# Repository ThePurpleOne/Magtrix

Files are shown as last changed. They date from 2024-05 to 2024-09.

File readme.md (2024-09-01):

---
Author : Jonas Stirnemann
Date : 2024
Title : Magnetic Board Game
Description : Board game etched directly on a PCB (Chess, Tic-Tac-Toe, etc.)
---

# Tic Tac Toe Board Game

PCB design for a Tic Tac Tie game. The game is played on a 3x3 grid, where the players have to align 3 of their pieces in a row, column or diagonal to win. The pieces are actual magnets that are moved by activating coils etched on the PCB.

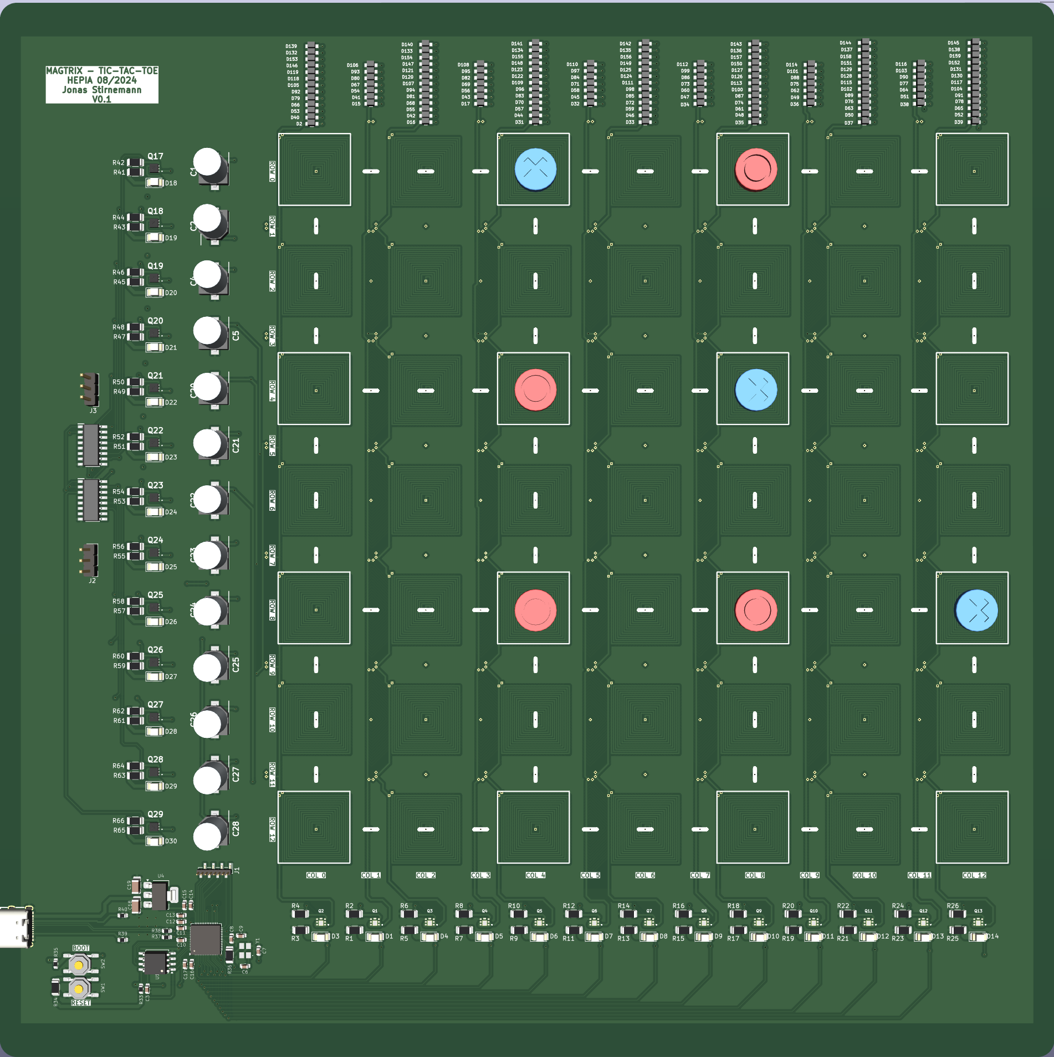
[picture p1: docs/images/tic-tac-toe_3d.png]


## Front end

The front end in React will display the game board and let the users play the game. The code can be found in [src/web/tictactoe/frontend](src/web/tictactoe/frontend)

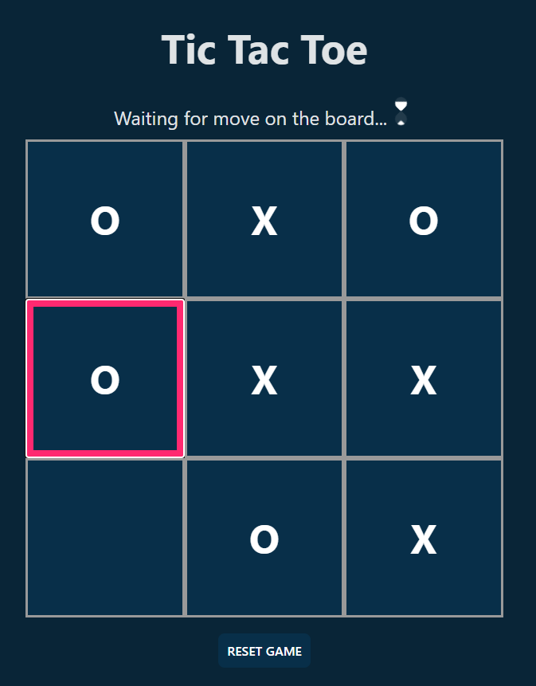
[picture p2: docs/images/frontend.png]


## Back end

The back end in Python will handle the communication with the actual board to tell it to make the moves and wait for an acknowledgement. The code can be found in [src/web/tictactoe/backend](src/web/tictactoe/backend)

## MCU Firmware

The firmware for the MCU will handle the communication with the back end to receive the moves. It will control the coils to move the pieces and tell the backend back when the move is done. The code can be found in [src/mcu/tictactoe](src/mcu/tictactoe)

## PCB

The PCB design is made in KiCad and can be found in [pcb/magtrix](pcb/magtrix)

Here's the schematics:

[docs/images/magtrix.pdf](docs/images/magtrix.pdf)

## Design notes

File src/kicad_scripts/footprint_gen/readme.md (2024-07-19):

# Footprint generation

This is a simple script to 2 types of coils with given parameters.

## Parameters

> Note : The coils are square.

- side_width: Width of the coil in both x and y direction.
- line_width: Width of the traces in the coil.
- spacing : Spacing between the traces.

> Note : The number of coils is determined by the side_width and spacing.

## Usage

The script can generate coils with specified layers.

The best choice on a 4 layer board is to use the top and third layers
for the main coils and second and bottom layers for the sub coils.
In a "sandwiched" configuration

```python
from square_coil import Coiler
if __name__ == "__main__":
    coiler = Coiler(side_width=8, line_width=0.3, spacing=0.2)

    coiler.create_and_save(
        name="coil",
        description="Test Coil",
        filename="top_coil",
        output_dir="outputs",
        layers=["F.Cu", "In2.Cu"],
    )

    coiler.create_and_save(
        name="coil",
        description="Test Coil",
        filename="sub_coil",
        output_dir="outputs",
        layers=["In1.Cu", "B.Cu"],
    )
```

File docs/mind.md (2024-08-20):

# Think 

- Add the characteristics that can be moved to enhance the torque
- why not use repulsion or both
- WHAT MAGNETS ??? Why not other Magnets, cubic better polarization for example 
- Multiple coils current direction

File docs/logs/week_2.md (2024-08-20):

---
Title : Week 2
Date : 21/05/2024 - 24/05/2024
---

# Question 1 : Are halbach array really usefull in our case ?

[https://www.duramag.com/techtalk/halbach-arrays/benefits-and-drawbacks-to-using-halbach-arrays/](https://www.duramag.com/techtalk/halbach-arrays/benefits-and-drawbacks-to-using-halbach-arrays/)

# Question 2 : Compute the distance a magnet could be attracted at, using a certain coil.
- Need to compute the magnetic field (B) generated by a coil with a specific current at a specific spot.
- Get the magnet's moment (m) and the distance, looks like we can get it from datasheet or by calculating it. [https://www.e-magnetica.pl/doku.php/magnetic_dipole_moment](https://www.e-magnetica.pl/doku.php/magnetic_dipole_moment)
- Should be able to compute the force from the coil on the magnet
- Shear force is different from adhesion force [https://www.supermagnete.ch/fre/faq/Quelle-est-la-difference-entre-force-d-adherence-et-force-de-cisaillement-force-de-deplacement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](https://www.supermagnete.ch/fre/faq/Quelle-est-la-difference-entre-force-d-adherence-et-force-de-cisaillement-force-de-deplacement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)

# Question 3 : Influence of the coil's shape on the magnetic field
- More turn means more magnetic field but also more resistance thus less current for the same voltage.
- The shape of the coil seems to influence the magnetic field, look for sources ?
- The coil's shape also influences the direction of the magnetic field, could we use that to our advantage ?

# Question 4 : Are linear line coils optimal ?
- The movement are freeer in linear line coils, but it would be harder to know where the magnet exactly are and it would be harder, not to grab other magnets when moving any one.

# MAGNETS

[https://www.supermagnete.ch/fre/aimants-disques-neodyme/disque-magnetique-10mm-1.5mm_S-10-1.5-N](https://www.supermagnete.ch/fre/aimants-disques-neodyme/disque-magnetique-10mm-1.5mm_S-10-1.5-N)

# COIL GENERATION IN KICAD
We can use a simple plugin integrated in Kicad to generate a coil with desired parameters. 

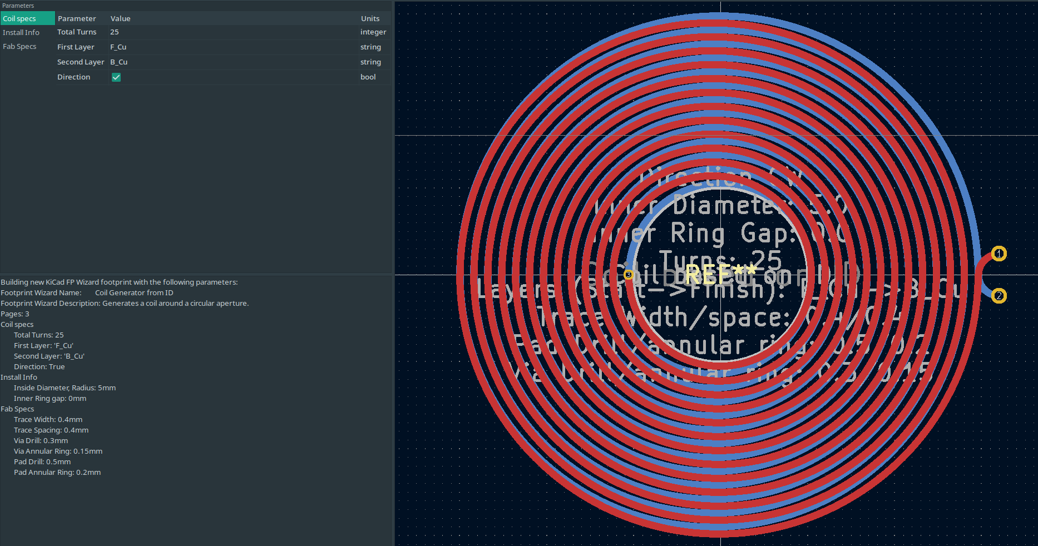
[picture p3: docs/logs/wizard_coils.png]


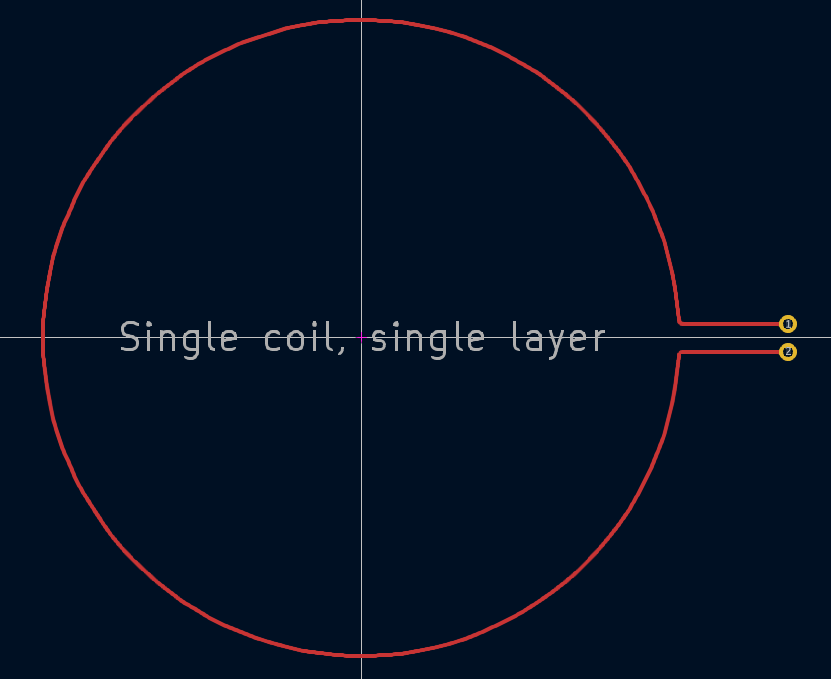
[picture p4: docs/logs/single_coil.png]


## Simulation
With the help of `kiutils` library, we can export the points forming the footprints of the coil.

> Here's an image of a simple coil with only 1 turn.
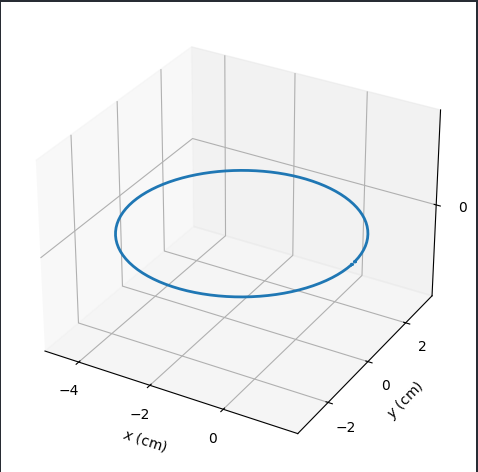
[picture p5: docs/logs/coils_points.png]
Image of points
> 

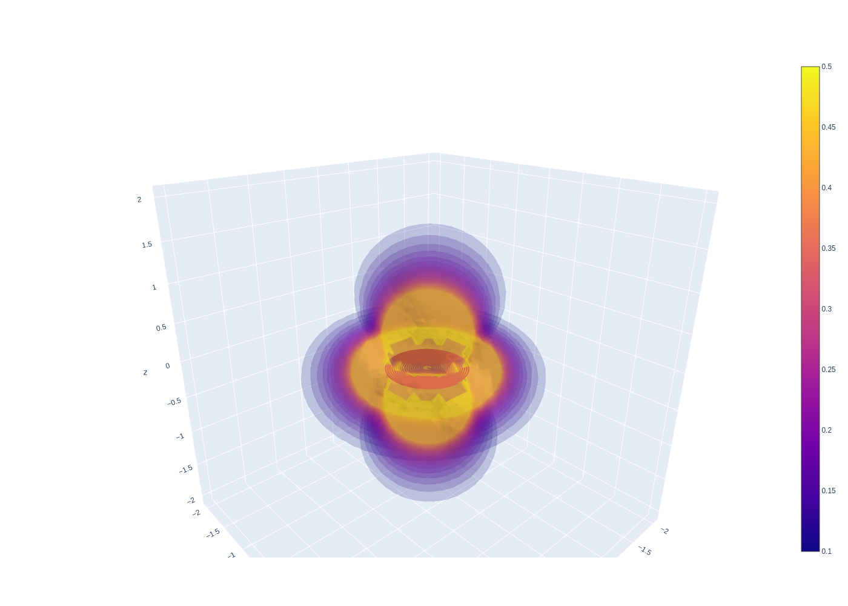
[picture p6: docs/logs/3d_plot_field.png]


## Helmholtz coils

[https://en.wikipedia.org/wiki/Helmholtz_coil](https://en.wikipedia.org/wiki/Helmholtz_coil)

# GENERAL sources
[Encyclopedia](https://www.e-magnetica.pl/doku.php/start)

[Selfmoving Chess Piece Pawn Makes Room](https://www.youtube.com/shorts/qu3ETY4ECMg
)

[Lab 5: The Biot-Savart law - magnetic
fields due to current carrying coils](http://www.yorku.ca/marko/PHYS2211/Lab5.pdf)

[Lorentz Force Law and Biot-Savart](https://andrealommen.github.io/PHY309/lectures/lorentz)

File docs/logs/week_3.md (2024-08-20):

---
Title : Week 3
Date : 28/05/2024 - 31/05/2024
---

# Breadboard proto for linear coils tests

I've made a simple schematics and mounted it on a breadboard to test the coils.

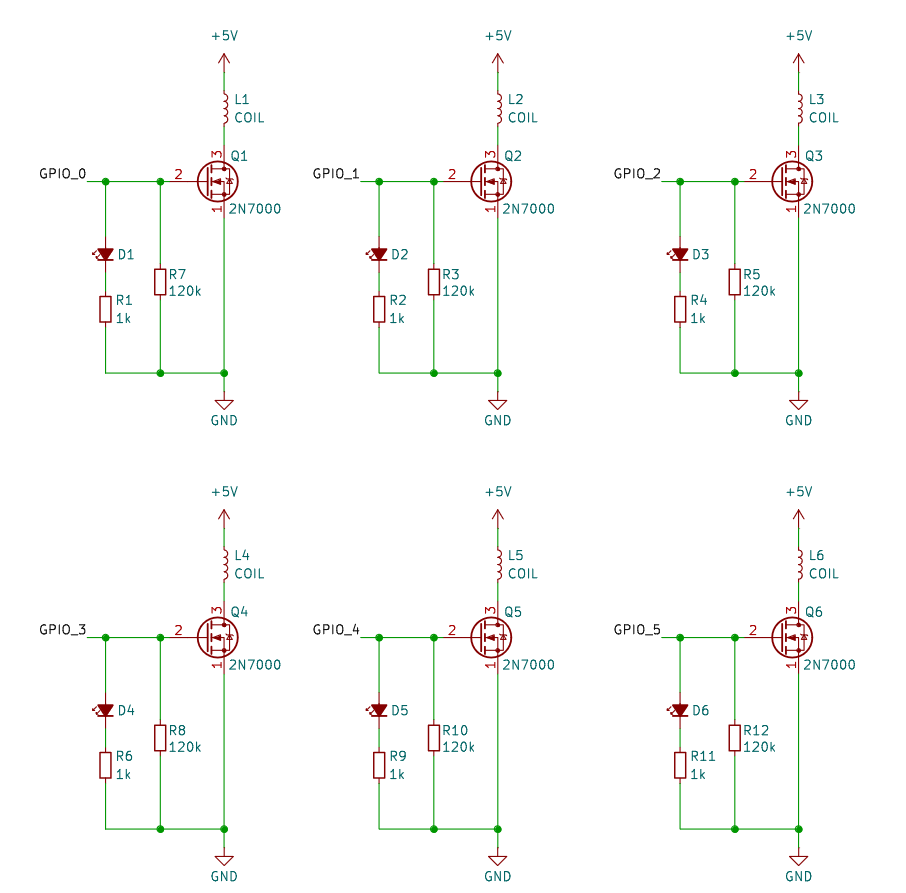
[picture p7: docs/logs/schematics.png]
Schematics


I mounted it with some 2N7000 Q1 N-Channel MOSFETs, controlled via a Raspberry Pi Pico.

```py
import digitalio
import board
import time

pins = [board.GP0, board.GP1, board.GP2, board.GP3, board.GP4, board.GP5, ]

coils = [digitalio.DigitalInOut(pin) for pin in pins]

for coil in coils:
	coil.direction = digitalio.Direction.OUTPUT

coils[3].value = True

print("STARTING TEST")
while True:
	# Set coils 0 to 2 to true one at the time
	for i in range(3):
		coils[i].value = True
		print(f"Coil {i} ON")
		time.sleep(0.3)
		coils[i].value = False
		print(f"Coil {i} OFF")

```

I could see the magnet jitter a bit but without moving, I tried cranking the power up. But aparts from heating more, it did not move better. The fets were getting hot because they were not dimensioned for the current. So i tried with bigger ones. 

I then tried with IRLZ14 N-Channel MOSFETs, but the results were the same. I stopped the test to avoid damaging the power supply and the transistors because i did not have proper flyback diodes.

# Began schematics with driver + flyback diodes and round coils

## Needs
I need:
- Big transistors capable of handling the current
- Flyback diodes to protect over voltage
- Series diodes with the coils to protect the power supply from the back EMF
- Optocouplers to isolate the driver from the Raspberry Pi Pico

## Choices

### Transistors MDD50N03D

I chose the MDD50N03D N-Channel MOSFETs:
- 38 W power dissipation
- 50 A continuous drain current
- 150 A pulsed drain current
- 30 V drain-source voltage

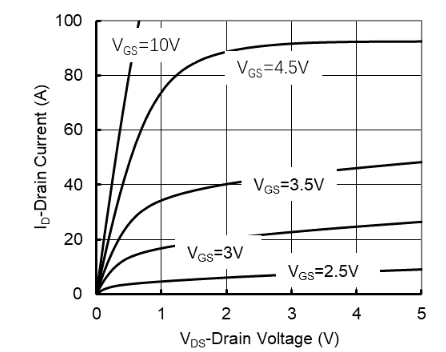
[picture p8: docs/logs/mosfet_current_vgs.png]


With a VGS of 3.3V outputed by the, we can obtain around 20 Amps of current with 0 ohm resistance...

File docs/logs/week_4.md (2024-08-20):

---
Title : Week 3
Date : 04/06/2024 - 07/06/2024
---

# Breadboard proto for linear coils with diodes

I just noticed that the transistors i was using were mixed and some of them were PMOS and others NMOS... 

I remade the schematics and mounted it on a breadboard to test the coils with only the PMOS, sadly...

PMOS is the **IRF9Z34**. 

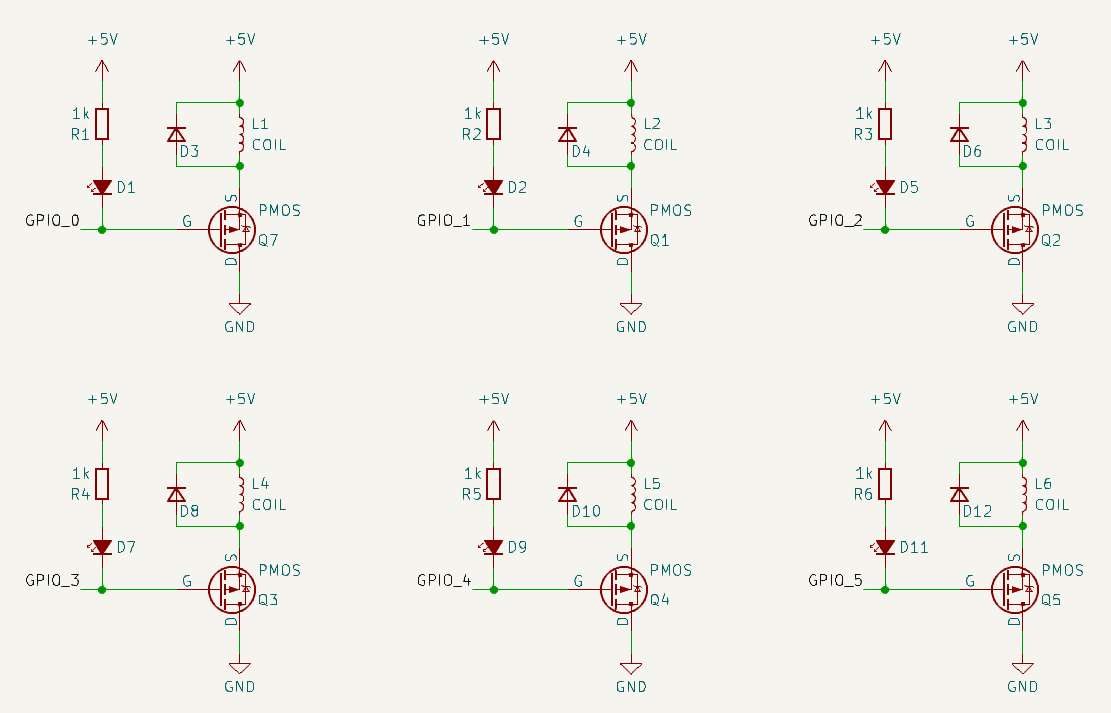
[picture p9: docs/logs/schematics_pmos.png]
Schematics


Pinout of the PMOS : 

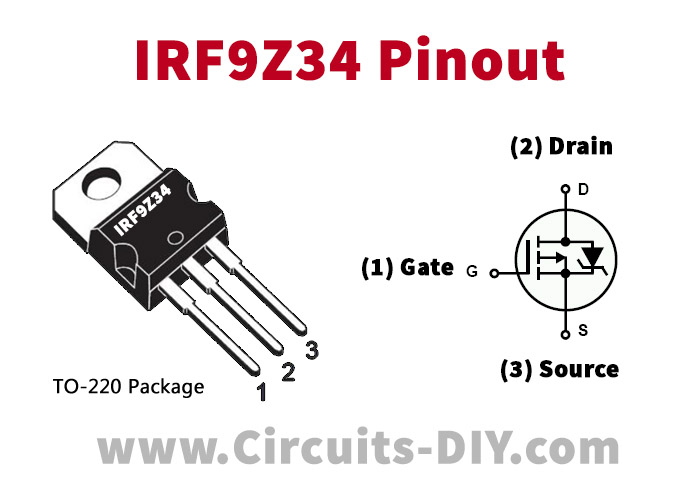
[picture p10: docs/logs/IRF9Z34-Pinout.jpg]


The magnet is moving with a delay of 0.3 between each coil activation. On the small board from PEMi Tech.

[https://hackaday.io/project/154496-2d-actuator-move-micro-robot-in-xy-2d-space](https://hackaday.io/project/154496-2d-actuator-move-micro-robot-in-xy-2d-space)

```py
import digitalio
import board
import time

pins = [board.GP0, board.GP1, board.GP2, board.GP3, board.GP4, board.GP5, ]

coils = [digitalio.DigitalInOut(pin) for pin in pins]

for coil in coils:
	coil.direction = digitalio.Direction.OUTPUT

coils[3].value = True

print("STARTING TEST")
while True:
	# Set coils 0 to 2 to true one at the time
	for i in range(3):
		coils[i].value = False
		print(f"Coil {i} ON")
		time.sleep(0.3)
		coils[i].value = True
		print(f"Coil {i} OFF")
```

But it's moving quiete poorly at low power: 5V (depending on the resistance)

When i crank the power up (10V and the coils draw about 1A), the magnet is moving better but the transistors are getting really hot and i have to stop the test to avoid damaging them.

From what i calculated, with 10V and 1A, the power dissipated by the transistors is 10W.



With this transistor, with a junction to ambient resistance of about 60 °C/W, the temperature should get to more than 600°C lol   

# Old PCB testing

I detached on part of the old PCB to test the it. It was not maintained properly,there was hot glue holding it together and some wires were soldered by hand

# PCB design

## Resistance of the round coils

In order to get a proper transistor that can handle the power, i need to know the resistance of the coils.

I compute the lenght of the spiral with the archimedean spiral formula on a website [https://www.omnicalculator.com/math/spiral-length](https://www.omnicalculator.com/math/spiral-length):

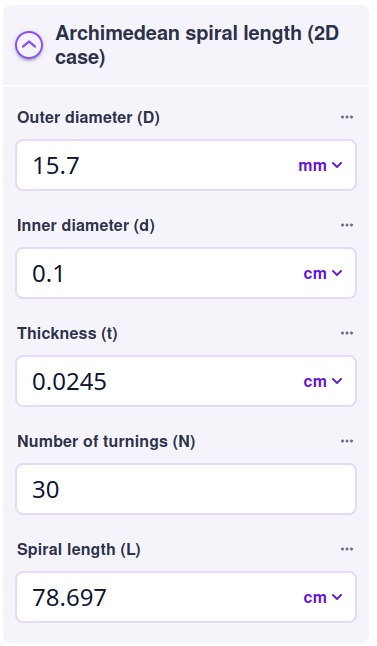
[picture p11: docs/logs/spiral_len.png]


We have a lenght of `78.697` cm for the spiral.

I can now compute the approximate resistance with an online calculator [https://www.allaboutcircuits.com/tools/trace-resistance-calculator/](https://www.allaboutcircuits.com/tools/trace-resistance-calculator/)

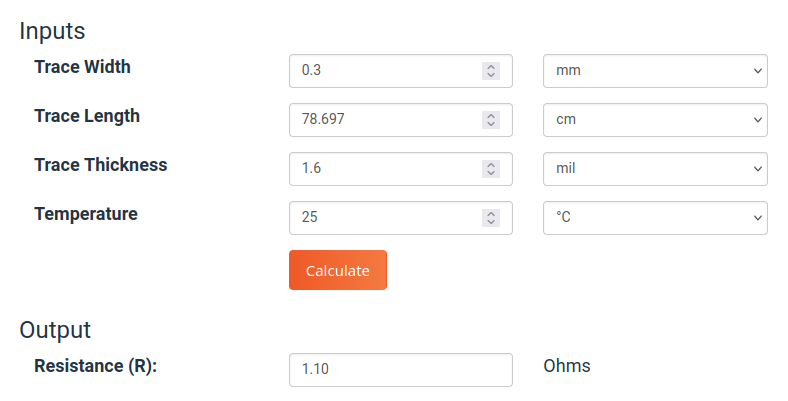
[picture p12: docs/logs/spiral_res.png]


The resistance is about `1.1 ohm`. Taking the via and traces coming to the coil into account, i can approximate the resistance to maximum `10 ohms` and minimum `1 ohm`.

We want to have a maximum amount of power in the coil while still not burning the transistors.

From what i've seen, power transistors have a junction to ambient resistance

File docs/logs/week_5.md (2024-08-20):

---
Title : Week 5
Date : 11/06/2024 - 14/06/2024
---

The 8mm circle magnets only move when applying massive power to the coils (50W...) and i cannot test properly since the transistors are getting really hot.

The 2mm square magnets are moving with 20W but the transistors are getting hot too.

# Solution 1
Find a transistor system that can handle the power, maybe add a heatsink.

# Solution 2
Find smaller magnet (preferably circle) that can be moved with less power. 

# Solution 3 ?
Multiple magnets in a 3d printed piece ? rom what

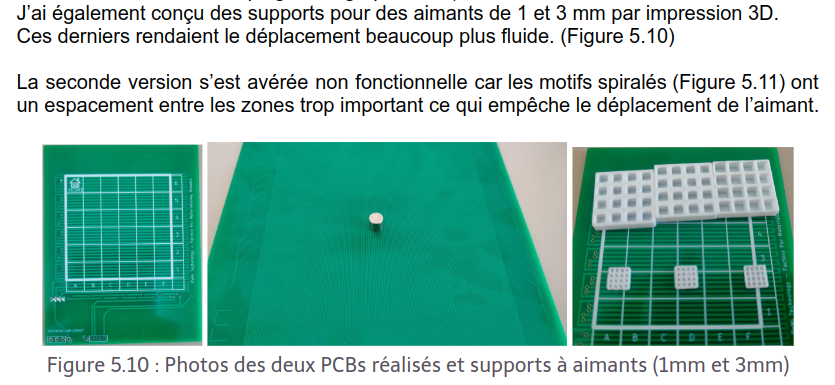
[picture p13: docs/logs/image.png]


# Insane planar motors from Rockwell

[Video demo planar motor](https://www.youtube.com/watch?v=xM1i5vORH4k)

[Actual planar motor site](https://planarmotor.com/en/overview)

# Some papers about 2d XY planar motors
[Papers directory](PAPERS/)

# PCB Specifications

- 2 or 4 layer board depending on possible thickness
- 6 driver transistors
- 4 different coil designs for testing
- Each design can access the 6 transistors
- 10x10mm coil areas

## Coil design 1
- Only 2 different coils per layer (A and B for layer 1 and C, D for layer 2 same as bobricius)
- **10** mils gaps and **20** mils traces (same as bobricius)

## Coil design 2
- 3 different coils per layer (A, B, C for layer 1 and D, E, F for layer 2)
- **10** mils gaps and **20** mils traces (same as bobricius)

## Coil design 3
- Only 2 different coils per layer (A and B for layer 1 and C, D for layer 2 same as bobricius)
- **10** mils gaps and **40** mils traces (same as bobricius)

## Coil design 4
- Only 2 different coils per layer (A and B for layer 1 and C, D for layer 2 same as bobricius)
- **40** mils gaps and **40** mils traces (same as bobricius)

# Components choice

## Transistors

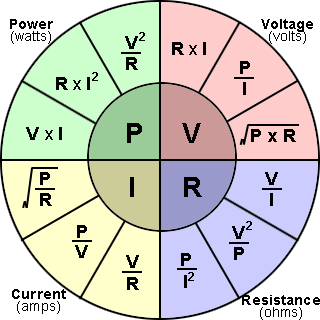
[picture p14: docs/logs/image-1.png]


With the `BUK6D120-40EX` transistor, rdson at 250 ohm:
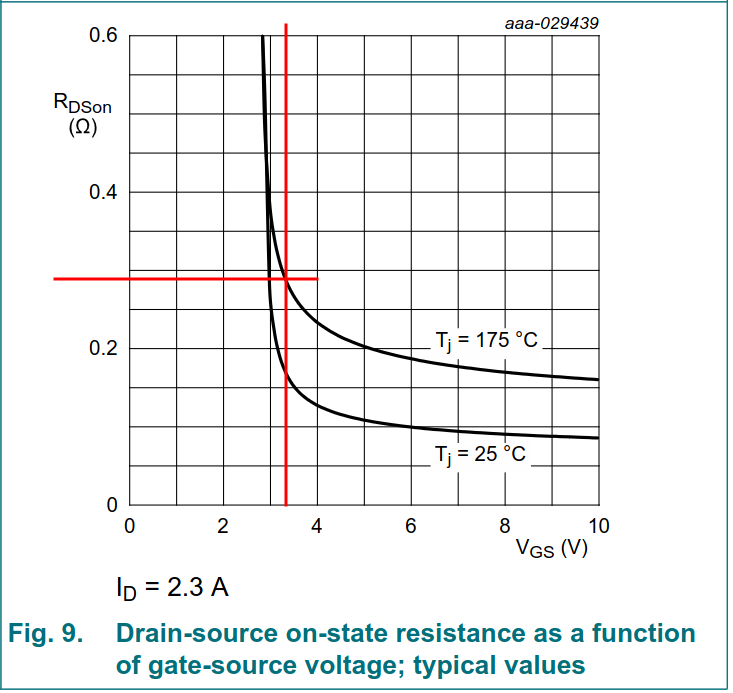
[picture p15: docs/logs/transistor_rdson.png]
RDS ON BUK6D120-40EX


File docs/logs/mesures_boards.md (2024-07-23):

# Sub coils
> Round sub coils between the main coils.

Drawing lots of current at 100%, reduced to 60-70% with a PWM 

Max temperature : 80°C (Thermal camera)

8mm Magnet 

## Code
```py
import digitalio
import board
import time
import pwmio

pins = [board.GP0, board.GP1, board.GP2, board.GP3, board.GP4, board.GP5, ]

coils = [pwmio.PWMOut(pin, frequency=50000) for pin in pins]

for coil in coils:
    coil.duty_cycle = 0

print("STARTING TEST")

while True:
    for i in range(6):
        coils[i].duty_cycle = 40000
        print(f"Coil {i} ON")
        time.sleep(0.3)
        
        coils[i].duty_cycle = 0
        print(f"Coil {i} OFF")
        time.sleep(0.2)

    for i in range(5, -1, -1):
        coils[i].duty_cycle = 40000
        print(f"Coil {i} ON")
        time.sleep(0.3)

        coils[i].duty_cycle = 0
        print(f"Coil {i} OFF")
        time.sleep(0.2)
```

## Status
Working almost fine!

# Layered coils

> 4 layers per coil

Max temperature : 65°C (Thermal camera)

Not drawing as much current as the sub coils, PWM almost max, not moving at all from one to another...

# SUB COILS SQUARE

> Square sub coils between the main coils, everythin is the same size and square.

Max temperature : 85°C after a long test (Thermal camera)

8mm Magnet

## Code
```py
# Testing the 4 boards
 
import digitalio
import board
import time
import pwmio

pins = [board.GP0, board.GP1, board.GP2, board.GP3, board.GP4, board.GP5, ]

coils = [pwmio.PWMOut(pin, frequency=50000) for pin in pins]

for coil in coils:
    coil.duty_cycle = 0

print("STARTING TEST")

ACTIVE_TIME = 0.5
INACTIVE_TIME = 0.1

while True:
    for i in range(6):
        coils[i].duty_cycle = 65000
        print(f"Coil {i} ON")
        time.sleep(0.4)
        
        coils[i].duty_cycle = 0
        print(f"Coil {i} OFF")
        #time.sleep(0.2)

    for i in range(4, -1, -1): # 4 to skip the second F
        coils[i].duty_cycle = 65000
        print(f"Coil {i} ON")
        time.sleep(0.3)

        coils[i].duty_cycle = 0
        print(f"Coil {i} OFF")
        #time.sleep(0.2)
```

## Status

Working really well, excepted the F position where it cannot hold enough the magnet

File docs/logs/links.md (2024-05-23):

# Links
- `2D stepper motor etched on PCB - micro manipulator` : https://hackaday.io/project/164507-2d-stepper-motor-etched-on-pcb-micro-manipulator
- `FLEXIBLE linear actuator` : https://hackaday.io/project/164263/gallery#71059ca11f0624f3184a775c98f448b2 
- `Hallbach array` : https://fr.wikipedia.org/wiki/Réseau_de_Halbach
- `Blog about making Hallbach array` : https://www.kjmagnetics.com/blog.asp?p=halbach-arrays
- `The Benefits and Drawbacks to Using Halbach Array Designs and Configurations` : https://www.duramag.com/techtalk/halbach-arrays/benefits-and-drawbacks-to-using-halbach-arrays/

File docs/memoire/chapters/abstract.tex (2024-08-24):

%% Tex spellcheck = fr_FR
\thispagestyle{noheader}
\chapter*{Abstract} % No (numbered) toc entry with *

\tikz[remember picture,overlay] \node[shift={(4.165cm,-1.955cm)}]
at (current page.north west)
{};
\tikz[remember picture,overlay] \node[shift={(-4.238cm,-1.97cm)}]
at (current page.north east)
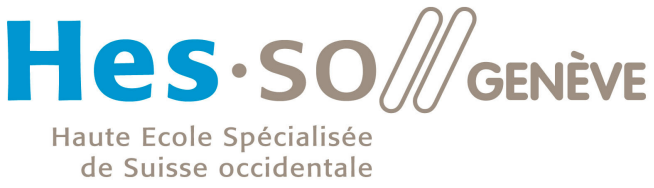
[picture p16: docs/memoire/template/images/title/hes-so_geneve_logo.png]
{};

\addcontentsline{toc}{chapter}{Abstract} % Adding toc entry
\thispagestyle{noheader}

\begin{spacing}{0.956}
	\vspace{0.5cm}

	When chess enthusiasts want to watch grandmaster games live, they often rely on computer screens. This project aims to bring board games back to the physical world by developing a board that can automatically move pieces. Controlled by a computer, it can be connected to any API, the board can be used for real-time game tracking or play. While this thesis focuses on a Tic-Tac-Toe game, the core technology is adaptable to any board game, with potential for scaling the board size as needed.
	The project involved designing a PCB, developing firmware, and creating a simple web app. The key innovation is using coils etched onto the PCB to attract pieces embedded with magnets. The process included testing various coil designs to find the most effective one and ensuring scalable control options. The final product is a Tic-Tac-Toe board with a 3x3 playable zone  and storage for pieces that have not yet been placed. It also comes with a full web-based interface to control the game via a backend communicating with the board via serial. Despite some minor issues that required manual adjustments, the project demonstrates significant potential for future expansion and application. The actual concept works with a single magnet but when trying to play with multiple bare magnets, the attraction between them is too strong and make the game unplayable since they attract each other. The issue could probably be resolved by using a different pieces design or by making the inter magnet distance bigger.

	%In the era of autonomous drones and \gls{uav}, there is a pressing need among constructors and major technology firms to establish a robust testing framework that ensures safety, reliability, cost-effectiveness, repeatability, and control, all while providing easily quantifiable metrics. This project endeavors to meet these demands by developing a sophisticated \gls{gnss} spoofer utilizing \gls{sdr} technology. The primary objective is to fabricate fake \gls{gnss} signals capable of deceiving drones into perceiving forward movement, even when they are stationary in front of an artificial obstacle, such as a fan wall. The overarching goal of this system is to create a controlled testing environment for \gls{uav}, facilitating the assessment and quantification of their flying performance metrics. By employing high-frequency position tracking alongside precise control over wind speed and \gls{gnss} signals, the system enables \gls{uav} to hover in place while experiencing simulated forward motion. This setup provides a comprehensive means of evaluating the \gls{uav}'s response and performance under dynamic conditions, without the need for costly and potentially hazardous outdoor testing scenarios. The proposed system promises to revolutionize \gls{uav} testing procedures by offering a safe, repeatable, and cost-effective solution that can be tailored to specific testing requirements. Moreover, its ability to generate easily quantifiable metrics ensures that developers and engineers can accurately assess the performance of \gls{uav} across various flight scenarios. Ultimately, this innovation holds the potential to accelerate advancements in autonomous drone technology by providing a reliable testing platform that accurately reflects real-world challenges.

	\vfill
	\begin{center}
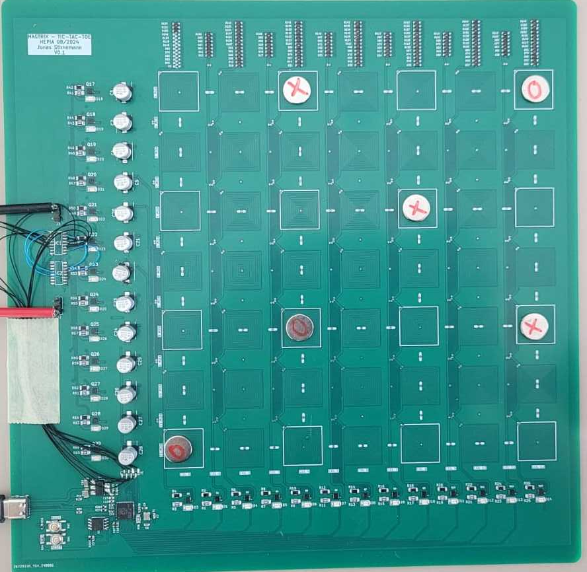
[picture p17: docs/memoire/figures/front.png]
		{}\\*
		\vfill
		%% CONTENT ENDS HERE

		{
			%%%%%%%%%%%%%%%%%%%%%%%%%%%%%%%%%%%%%%%%%%%%%%%%%%%%%%%%%%%%%%%%%%%%%%%%%%%%%%%%
			%%%%%%%%%%%%%%%%%%%%%%%%%% DO NOT MODIFY THE TABLE BELOW %%%%%%%%%%%%%%%%%%%%%%%
			%%%%%%%%%%%%%%%%%%%%%%%%%%%%%%%%%%%%%%%%%%%%%%%%%%%%%%%%%%%%%%%%%%%%%%%%%%%%%%%%
			\begin{tabular*}{16cm}{p{7.59cm} p{7.58cm}}
				\small Candidate:					&	\small Professor:\\*[10pt]
				\small\textbf{\textsc{\Author}}		&	\small\textbf{\textsc{\Professor}}\\*[10pt]
				\footnotesize  Branch : ISC	&	\footnotesize  \textbf{In collaboration with:}  \\*[10pt]
				\footnotesize  {} & \footnotesize  Thesis subject to an internship agreement: \Convention\\*[20pt]
				\footnotesize  {} & \footnotesize  Work subject to confidentiality agreement: \Confidentiel\\*[10pt]
			\end{tabular*}\\*[1.9cm]
		}

	\end{center}
\end{spacing}

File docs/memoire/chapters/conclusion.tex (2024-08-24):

%% Tex spellcheck = fr_FR
\chapter*{Conclusion}
\addcontentsline{toc}{chapter}{Conclusion} % Adding toc entry

This thesis presents a proof of concept for a scalable, automated board game system that integrates PCB-based electromagnetics, offering a novel approach to bringing digital game tracking into the physical world. Initially focused on a Tic-Tac-Toe game, the project successfully demonstrated the ability to move game pieces automatically via coils etched directly onto the PCB, controlled by a web application.

The iterative process of coil design and control system development highlighted the potential of this technology to be adapted for more complex games like chess, with minimal adjustments. The final prototype, a 3x3 Tic-Tac-Toe board, effectively showcases the concept’s viability, despite some hardware imperfections.

While the current implementation is limited to Tic-Tac-Toe, the core technology is designed with scalability in mind, offering possibilities for expansion into larger and more intricate board games. The project's been succesful in automating game piece movement through electromagnetism, but further development is needed to address issues with multiple bare magnets interacting with each other. The game is not fully playable as multiple magnets are needed.

The simulation of coil designs proved challenging, as I was unable to achieve results that matched real-world outcomes. This discrepancy primarily came from limited expertise in electromagnetism and the inherent complexity of the simulations. As a result, the design process relied heavily on a trial-and-error approach. A more in-depth theoretical understanding of electromagnetism would likely have led to more accurate simulations and a more efficient identification of the optimal coil design. Moving forward, strengthening the theoretical foundation in this area could greatly enhance the design process, leading to more precise and reliable outcomes.

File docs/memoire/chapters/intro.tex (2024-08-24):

%% Tex spellcheck = fr_FR
\chapter*{Introduction}
\addcontentsline{toc}{chapter}{Introduction} % Adding toc entry

As the final step in our Bachelor's program in Computing and Communication Systems at \gls{hepia}, we undertake a Bachelor project that spans 14 weeks immediately following our last semester. It extends for a period of 14 weeks during which a workload of 450 hours is expected. This project is the culmination of our studies and is intended to demonstrate our ability to apply the knowledge and skills acquired during our studies to a concrete problem.

% Project is a magnetic tic tac toe
Our initial project concept was to design and implement a \gls{pcb}-based chessboard, where chess pieces are moved using magnetic fields generated by electromagnets directly etched onto the \gls{pcb}. However, due to the complexity involved in implementing, producing, shipping, and using a chessboard of this nature, we decided to shift our focus to another board game—Tic-Tac-Toe—that shares similar concepts but offers a more manageable form factor. Should there be a need, the project can be scaled up to a chessboard with minimal adjustments, extending the board and reprogramming the game rules.

Tic-Tac-Toe is a simple game played on a 3x3 grid, where two players take turns placing their pieces on the board. The objective is to be the first to align three pieces in a row, column, or diagonal. Our implementation of this game eliminates the need for physical interaction with the board. The pieces, embedded with magnets, are moved by electromagnets that are etched onto the \gls{pcb}.

\begin{figure}[H]
	\centering
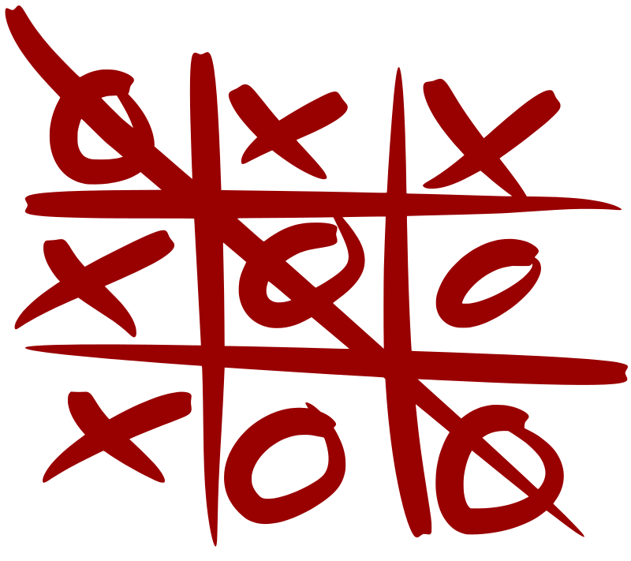
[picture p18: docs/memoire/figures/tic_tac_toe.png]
	
	\caption[Tic Tac Toe example]{Tic Tac Toe example}
	\label{fig:tictactoe_game}
\end{figure}

Players interact solely through a web application, which displays the game board and enables them to make their moves. This application communicates with a backend, which in turn connects to a microcontroller responsible for controlling the electromagnets. The microcontroller activates the coils in a specific sequence to move the pieces on the board.

% Why this project
The project was chosen because it combines several aspects of our studies, such as electronics, software development and microcontroller programming. It also allows us to work on a project from start to finish, from the design phase to the implementation and testing phase. The project is also interesting because it involves the use of different technologies as \gls{pcb} design, microcontroller programming, and web development.

% Objectives
The primary objective of this project is to design and implement a functional, automated Tic-Tac-Toe board that utilizes electromagnetism to move the pieces, completely eliminating the need for manual interaction. While the project focuses on a simple game like Tic-Tac-Toe, it serves as a proof of concept for more complex games such as chess. In a chess setting, this technology could enable spectators to watch a grandmaster's game with the moves being replicated in real-time on a physical board, without anyone needing to physically move the pieces. Or it could be used for educational purposes, allowing students to play against a computer that moves the pieces for them.

% Structure
This thesis is organized into three main sections, each addressing a distinct aspect of the project. The first section explores the theoretical concepts of magnetism and electromagnetism, along with simulations conducted to validate the concept. The second section focuses on the iterative design process of the hardware to identify the optimal coil design. The third section details the final hardware design and the software components of the project.

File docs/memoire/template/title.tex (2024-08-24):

%% Tex spellcheck = fr_FR
%%%%%%%%%%%%%%%%%%%%%%%%%%%%%%%%%%%%%%%%%%%%%%%%%%%%%%%%%%%%%%%%%%%%%%%%%%%%%%%%
%%                                                                             %
%% HEPIA BACHELOR THESIS FRONTPAGE LATEX TEMPLATE                              %
%% version 0.9 - 2020/04/20                                                    %
%%                                                                             %
%% DO NOT MODIFIY THIS PAGE                                                    %
%%                                                                             %
%%%%%%%%%%%%%%%%%%%%%%%%%%%%%%%%%%%%%%%%%%%%%%%%%%%%%%%%%%%%%%%%%%%%%%%%%%%%%%%%
\begin{titlepage}
	\newgeometry{top=2cm,bottom=2cm,right=2cm,left=2cm}
	%% HEADER IMAGES
	\tikz[remember picture,overlay] \node[shift={(4.165cm,-1.955cm)}]
	at (current page.north west)
	{};
	\tikz[remember picture,overlay] \node[shift={(-4.238cm,-1.97cm)}]
	at (current page.north east)
	{};

	\begin{center}
		%% CONTENT STARTS HERE
		{\fontfamily{phv}\selectfont
		\vspace*{51pt}
		{
		%% TITLE
		\begin{spacing}{1.5}
			{\fontsize{16pt}{20pt} \textbf{\Title}}\\[29pt]
		\end{spacing}

		%% IMAGE IF ANY
		{\color{white}
		\\[35pt]
		%\includegraphics[height=8cm,width=8cm]{\TitleImage}\\[35pt]
		}

		%% PROJET DE SEMESTRE
		{\large Bachelor Thesis presented by}\\[21pt]

		%% AUTHOR
		{\fontsize{16pt}{20pt} \textbf{\Author}}\\[17pt]

		%% DEGREE
		{\large
		\fontsize{14pt}{20pt} \textbf{Computing and Communication Systems\\ \Orientation }\\[32pt]

		%% DATE
		\textbf{\Month, \Year}}\\[49pt]

		{
		\begin{tabular*}{16cm}{>{\centering}m{7.59cm}>{\centering}m{7.58cm}}
			%% SUPERVISOR
			Under the guidance of\\[13pt]
			\textbf{ \Professor }
			&
			%% CLIENT (IF ANY)
			Mandant\\[12pt]
			\textbf{ \Client }
		\end{tabular*}
		}
		}
		\vfill
		}%\fontfamily
	\end{center}
\end{titlepage}
\addtocounter{page}{1}

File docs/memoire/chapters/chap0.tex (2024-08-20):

%% Tex spellcheck
% Maybe put this as Chapter 2

% Write in English.
\chapter{Chapter 1 :  Technical concepts}

\section{Magnetism}

Magnetism \footcite{noauthor_nasa_magnetism} is a physical phenomenon produced by the motion of electric charge, resulting in attractive and repulsive forces between objects. The motion of electric charge creates a magnetic field, which exerts a force on other moving charges.

The concepts of magnetism and electromagnetism are essential to the project. The board's design must take into account the magnetic fields generated by the coils and the magnets' attraction to these fields. For that we need to understand the basics of magnetism and electromagnetism. Ampere's Law for example states that the line integral of the magnetic field \(\mathbf{B}\) around a closed loop is proportional to the total electric current \(I\) passing through the loop. Mathematically, it is expressed as:

\[
	\oint_{\mathcal{C}} \mathbf{B} \cdot d\mathbf{l} = \mu_0 I_{\text{enc}}
\]

where:
\begin{itemize}
	\item \(\oint_{\mathcal{C}} \mathbf{B} \cdot d\mathbf{l}\) is the line integral of the magnetic field around a closed path \(\mathcal{C}\),
	\item \(\mu_0\) is the permeability of free space \((\mu_0 \approx 4\pi \times 10^{-7} \, \text{T} \cdot \text{m/A})\),
	\item \(I_{\text{enc}}\) is the total current enclosed by the path (in Amperes) \(\mathcal{C}\).
\end{itemize}

\newpage

\subsection{Direction of the magnetic field}
The direction of the current passing through a wire determines the direction of the magnetic field around the wire. The right-hand rule is a common way to determine the direction of the magnetic field around a current-carrying wire. The rule states that if the thumb of the right hand points in the direction of the current, the fingers will curl in the direction of the magnetic field around the wire.

\begin{figure}[H]
	\centering
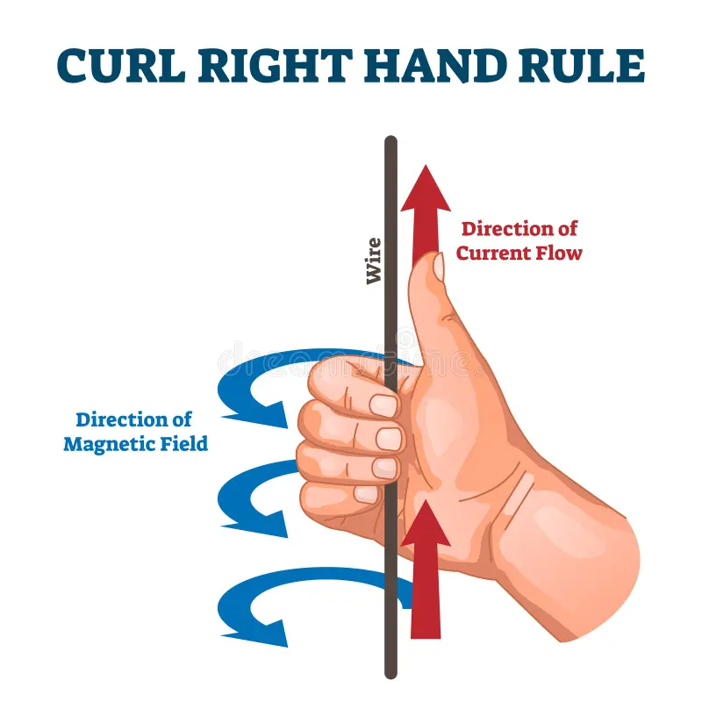
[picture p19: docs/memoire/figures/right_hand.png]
	
	\caption[Right hand rule]{Right hand rule Source: thumbs.dreamstime.com ref: URL08}
	\label{fig:right_hand_rule}
\end{figure}

\section{Permanant magnets}

Permanent magnets are materials that produce a magnetic field without the need for an external magnetic field. They are made of ferromagnetic materials such as iron, nickel, and cobalt. The magnetic field is created by the alignment of the magnetic domains in the material. The domains align in the same direction, creating a net magnetic field. The strength of the magnetic field depends on the material and the alignment of the domains.

The strength of the magnetic field is measured in units of Tesla (T) or Gauss (G). Stacking magnets can increase the magnetic field strength\footcite{noauthor_factors_nodate}. For example, stacking flat disc magnets multiplies the adhesive force until the stack reaches a height of half the diameter of a single disc magnet at a maximum.

For testing purposes, we tried multiple magnets of different sizes from Super Magnet Shop\footcite{noauthor_buy_nodate}. The magnets come with a datasheet that give us the magnetic field strength of the magnets as Residual magnetism Br 13200-13700 G, 1.32-1.37 T. This means for example that the magnetic field strength of this specific magnet is between 1.32 and 1.37 Tesla.

They also give us the polarization pattern of the magnet. For example the disk magnet has its poles on the flat faces of the disk.

\begin{figure}[H]
	\centering
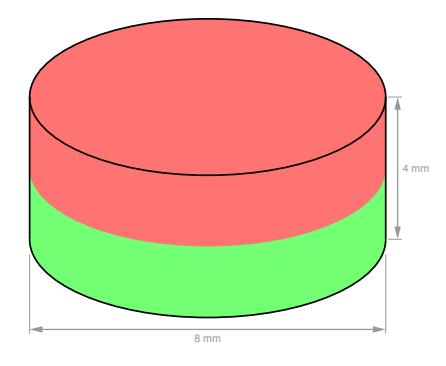
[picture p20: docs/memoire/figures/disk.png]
	
	\caption[Disk magnet polarity]{Disk magnet polarity Source: www.supermagnete.ch ref: URL09}
	\label{fig:disk}
\end{figure}

\begin{figure}[H]
	\centering
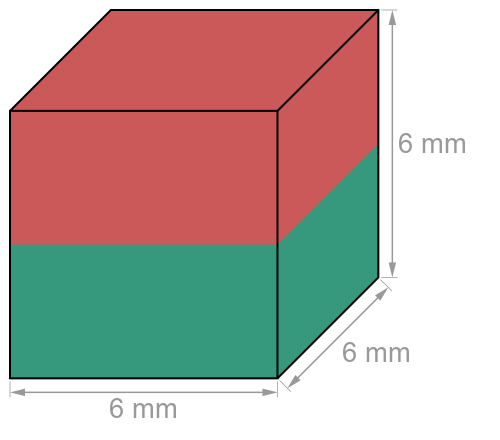
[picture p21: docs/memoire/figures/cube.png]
	
	\caption[Cube magnet polarity]{Cube magnet polarity Source: www.supermagnete.ch ref: URL09}
	\label{fig:cube}
\end{figure}

\section{Calculate the force of a magnetic field on a magnet}

To calculate the force exerted on a magnet by a magnetic field (for example from a pcb coil), taking into account friction and the magnet's mass, we can use the following formulas:

Calculate the Magnetic Force

\[
	F_{\text{mag}} = m \cdot B \cdot \sin(\theta)
\]

Calculate the Friction Force

\[
	F_{\text{friction}} = \mu \cdot m_{\text{weight}} \cdot g
\]

Calculate the Total Force

\[
	F_{\text{total}} = F_{\text{mag}} - F_{\text{friction}}
\]

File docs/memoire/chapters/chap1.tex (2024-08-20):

%% Tex spellcheck
% Maybe put this as Chapter 2

% Write in English.
\chapter{Chapter 2 : State of the art}

We want to use \gls{pcb} coils to move a magnet directly via the magnetic field generated by the coil. This concept is not new and has been used in some motor applications for example. There also is some people that use this concept for learning or entertainement purposes. This helped us to get some ideas on how to design our own system.

\section{PCB Motors}

There has been a huge interest in the development of \gls{pcb} motors. These motors are made by etching a coil pattern on a \gls{pcb} to act as the stator. There is a center shaft attached to magnets. When powering the coils in a specific sequence, the magnets will be attracted to the coils and the motor will rotate.

\begin{figure}[H]
	\centering
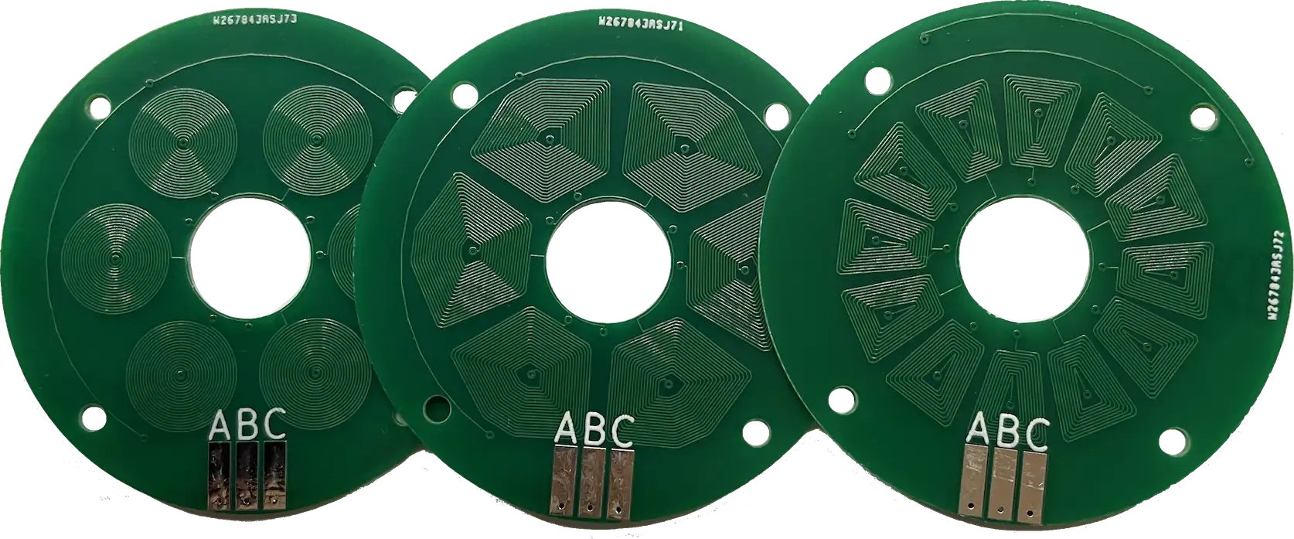
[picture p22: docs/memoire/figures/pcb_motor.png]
	
	\caption[\gls{pcb} Motor]{Atomic14 \gls{pcb} stators Source: https://www.atomic14.com ref: URL02}
	\label{fig:pcb_motor}
\end{figure}

There also is some commercial products that use this concept. They claim to be more efficient, Lighter with higher torque density. For example \footcite{noauthor_pcb_nodate} sells services and production to design your own \gls{pcb} motor with specified specs, and they use \gls{pcb} stators.

\begin{figure}[H]
	\centering
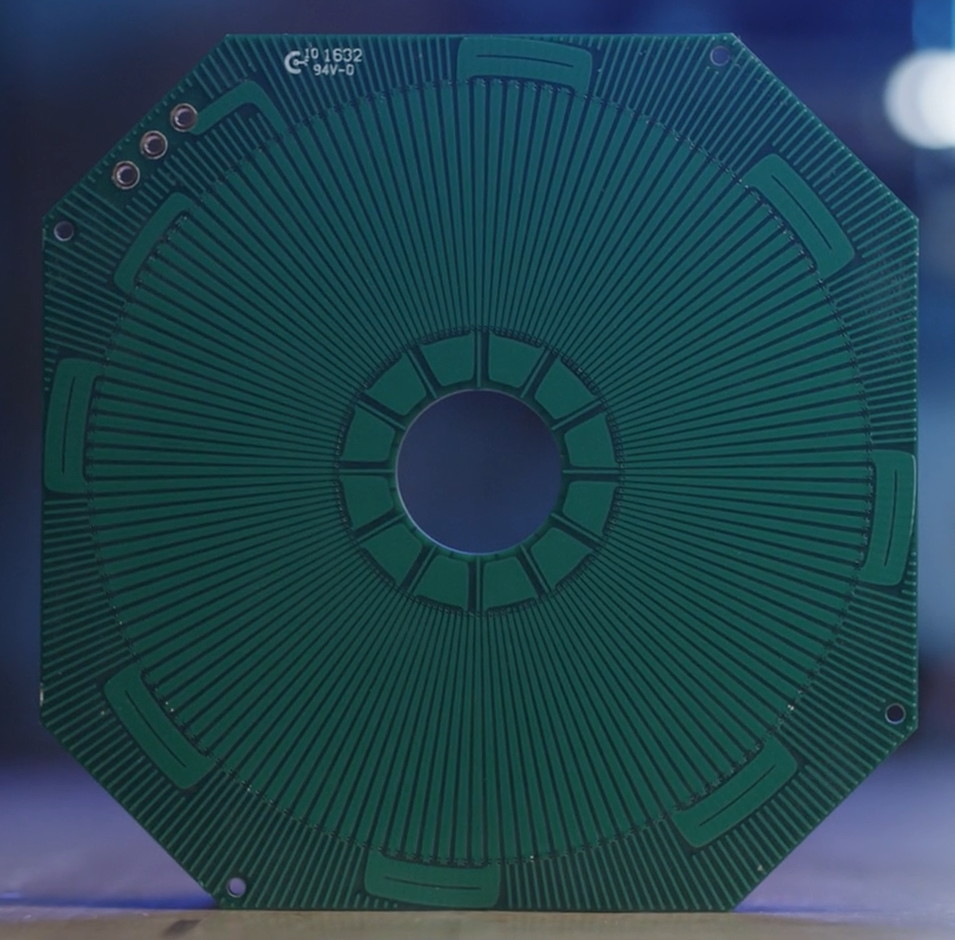
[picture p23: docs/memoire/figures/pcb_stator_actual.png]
	
	\caption[Commercial \gls{pcb} Motor's stator by ECM]{\gls{pcb} stator from EMC Source: https://pcbstator.com/ ref: URL03}
	\label{fig:pcb_stator}
\end{figure}

\begin{figure}[H]
	\centering
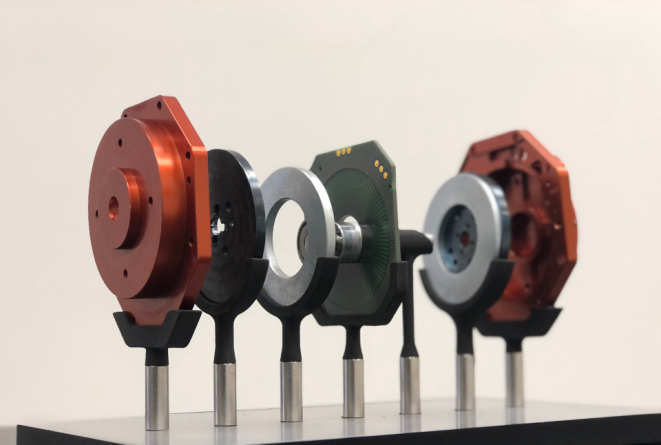
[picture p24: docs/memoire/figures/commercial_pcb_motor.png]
	
	\caption[Commercial \gls{pcb} Motor by ECM]{\gls{pcb} Stator's full motor design Source: https://pcbstator.com/ ref: URL04}
	\label{fig:pcb_stator_full}
\end{figure}

\section{PCB 2D linear actuators}

There are some people that have used the same concept to make a linear actuator. They use linear \gls{pcb} traces to move a magnet in a 2D linear fashion. There is for example a project on hackaday \footcite{noauthor_2d_nodate} that does just that. They actually use 3 different for each axis. They alternate those 3 coils made with \gls{pcb} traces to move the magnet in the desired direction.

The concept seems to have been developped and tested by SRI\footcite{sri_magnetically_2014} in 2014. They used a similar concept to move a micro robot in a 2D space.

\begin{figure}[H]
	\centering
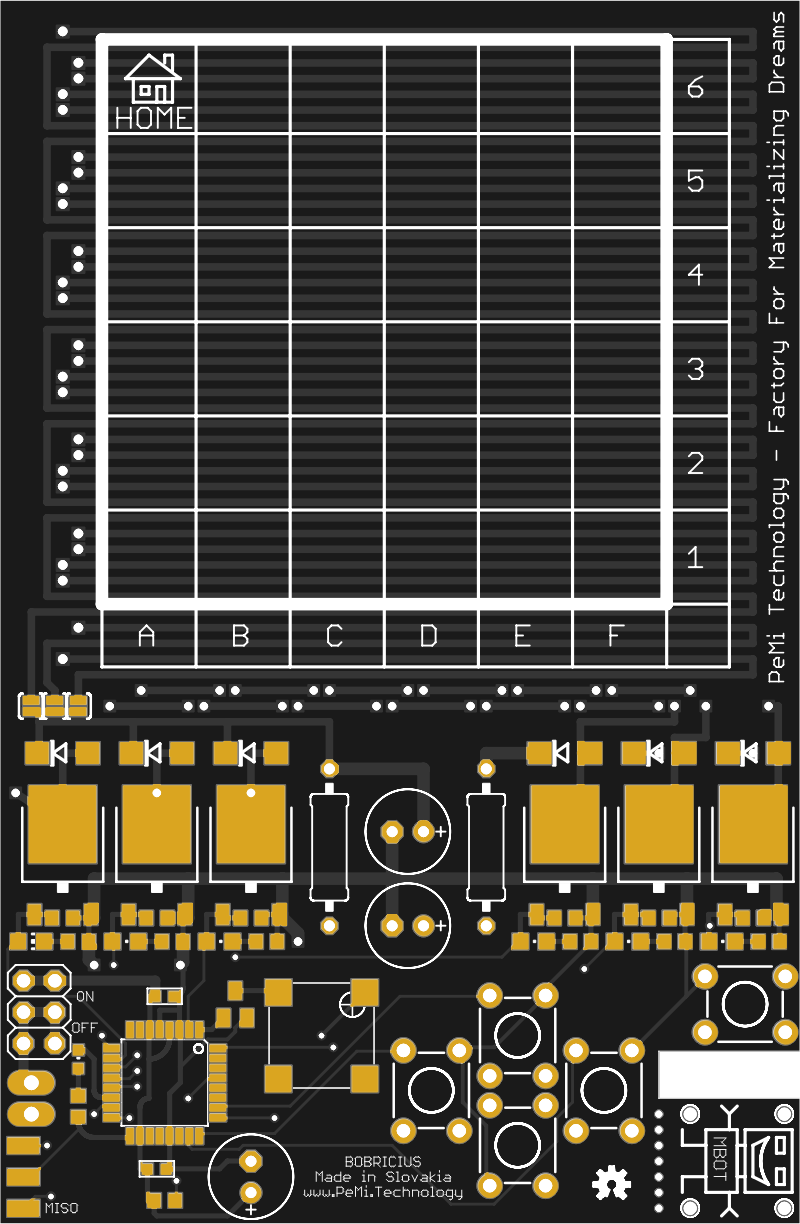
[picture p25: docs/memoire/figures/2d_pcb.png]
	
	\caption[2D X/Y \gls{pcb} actuator by Bobricius]{\gls{pcb} move a magnet in X/Y axis  Source: hackaday.io ref: URL06}
	\label{fig:2d_pcb}
\end{figure}

\begin{figure}[H]
	\centering
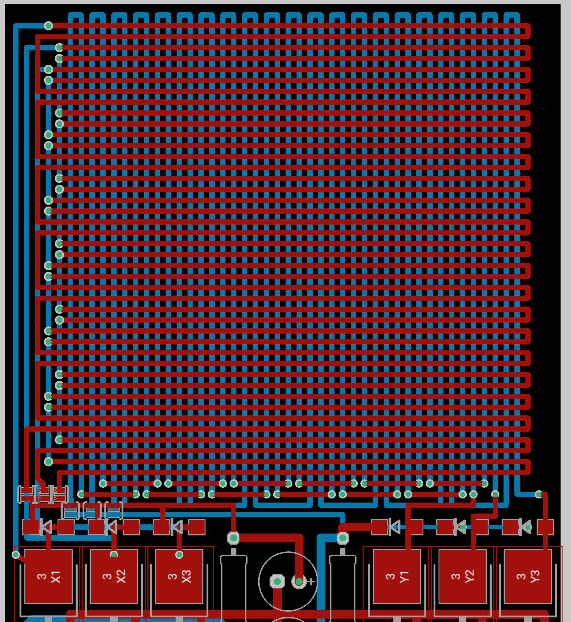
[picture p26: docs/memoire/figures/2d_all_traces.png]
	
	\caption[\gls{pcb} design 2D actuator]{\gls{pcb} design with linear coils Source: hackaday.io ref: URL06}
	\label{fig:2d_all_traces}
\end{figure}

We can see three different traces running on all the \gls{pcb} and alternating. There is three of these traces on the TOP layer of the \gls{pcb} and three on the BOTTOM layer. The magnet is moved by passing current through each coil one by one. The direction of the magnet is determined by the order of activation of the coils. So by activating the coils one then two then three, the magnet will move in one direction. By activating the coils three then two then one, the magnet will move in the opposite direction.

\begin{figure}[H]
	\centering
	
	\caption[\gls{pcb} design horizontal traces]{\gls{pcb} design with horizontal coils}
	\label{fig:2d_horizontal_traces}
\end{figure}

\begin{figure}[H]
	\centering
	
	\caption[\gls{pcb} design vertical traces]{\gls{pcb} design with vertical coils}
	\label{fig:2d_vertical_traces}
\end{figure}

\section{PCB coils}

Some projects use \gls{pcb} traces to draw arbitrary shaped coils like spirals or squares to generate a magnetic field. They can increase the torque by increasing the number of turns or current capacity (Bigger traces means less resistance, which means more current thus more magnetic field). They can also enhance the magnetic field by stacking multiple coils on the different \gls{pcb} layers.

Unlike the pcb stator motors where the magnets are on a free rotating shaft, the coils here have to generate enough force to attract the magnet while countering the friction between the magnet and the \gls{pcb}.

Carl Bugeja\footcite{noauthor_carl_nodate} has made a project where he uses a spiral coil to move a magnet in a linear path, he actually the design with FR4\footcite{noauthor_fr-4_2024} basic \gls{pcb} but also with flexible \gls{pcb}. He made a small video\footcite{carl_bugeja_actuating_2018} of the magnet moving on the \gls{pcb}. He mostly uses a Ball magnet to help reduce the friction between the magnet and the \gls{pcb}.

\begin{figure}[H]
	\centering
	
	\caption[\gls{pcb} coils design from Carl Bugeja]{\gls{pcb} design of spiraling coils that form a linear path for a magnet Source: hackaday.io ref: URL07}
	\label{fig:pcb_coils_spiral}
\end{figure}

%\begin{figure}[H]
%	\centering
%	\includegraphics[width=0.8\linewidth]{modulations.png}
%	\caption[Modulations]{Example of modulations Source: https://content.cdntwrk.com/ ref: URL06}
%	\label{fig:modulations}
%\end{figure}

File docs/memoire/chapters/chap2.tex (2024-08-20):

%% Tex spellcheck
% Maybe put this as Chapter 2

% Write in English.
\chapter{Chapter 3 : Simulations}

In this chapter, we will present the different simulations that were done to test the directivity and force of different coil shapes. There's is a wide variety diferrent software that can be used to simulate magnetic fields. I found Python scripting to be more versatile and easier to get the results I wanted.

The goal of these simulations is to determine if one shape is better than an other and if the magnetic field is strong enough to move a magnet. The simulations only take into account a fixed current of 1A and a number of turns in a determined area. We only really want the magnetic field in the X and Y direction as we will only move the magnet in a 2D space. But we should keep in mind that the Z direction might add some friction.

We'll do out calculations with a 6x6x6 cubic magnet with a magnetic field strength of 1.29T and a magnet weight of 1.6416 grams. We'll consider a friction coefficient of 0.2 for the magnet on the surface of the PCB.

In order to calculate the force of the magnetic field on the magnet, we'll need to compute the magnetic moment of a specific magnet, we need to know the volume of the magnet and the residual magnetism.

\begin{itemize}
	\item Residual magnetism: \( B_r = 1.29 \, \text{T} \)
	\item Side length of the cubic magnet: \( 6 \, \text{mm} = 0.006 \, \text{m} \)
\end{itemize}

The volume \( V \) of the cubic magnet is calculated as:
\[
	V = (\text{Side length})^3 = (0.006 \, \text{m})^3 = 2.16 \times 10^{-7} \, \text{m}^3
\]

The magnetic moment \( m \) is given by:
\[
	m = B_r \cdot V
\]
\[
	m = 1.29 \, \text{T} \times 2.16 \times 10^{-7} \, \text{m}^3
\]
\[
	m = 2.78 \times 10^{-7} \, \text{A} \cdot \text{m}^2
\]

\section{Linear coil}

\begin{figure}[H]
	\centering
	
	\caption[Simulation of a magnetic field in a simple wire]{Simulation of a simple wire in a 10mm x 10mm x 5mm zone, with a current of 1A}
	\label{fig:simu_simple_wire}
\end{figure}

As we can observe, the magnetic field is weak and gets weaker as we move away from the wire. We'll take a middle value of 8 uT at around 3mm from the wire.

Given data:
\begin{itemize}
	\item Magnetic flux density of the external field: \( B = 8 \, \mu\text{T} = 8 \times 10^{-6} \text{ T} \)
	\item Magnetic moment: \( m = 2.78 \times 10^{-7} \text{ A} \cdot \text{m}^2 \)
	\item Magnet weight: \( m_{\text{weight}} = 1.6416 \text{ g} = 0.0016416 \text{ kg} \)
	\item Coefficient of friction: \( \mu = 0.2 \)
	\item Acceleration due to gravity: \( g = 9.81 \text{ m/s}^2 \)
	\item Angle between magnetic moment and external field: \( \theta = 90^\circ \), so \( \sin(\theta) = 1 \)
\end{itemize}

Calculate the Magnetic Force

\[
	F_{\text{mag}} = m \cdot B \cdot \sin(\theta)
\]

\[
	F_{\text{mag}} = 2.78 \times 10^{-7} \, \text{A} \cdot \text{m}^2 \times 8 \times 10^{-6} \, \text{T}
\]

\[
	F_{\text{mag}} = 2.22 \times 10^{-12} \text{ N}
\]

Calculate the Friction Force

\[
	F_{\text{friction}} = \mu \cdot m_{\text{weight}} \cdot g
\]

\[
	F_{\text{friction}} = 0.2 \times 0.0016416 \text{ kg} \times 9.81 \text{ m/s}^2
\]

\[
	F_{\text{friction}} \approx 0.0032 \text{ N}
\]

Calculate the Total Force

\[
	F_{\text{total}} = F_{\text{mag}} - F_{\text{friction}}
\]

\[
	F_{\text{total}} = 2.22 \times 10^{-12} \text{ N} - 0.0032 \text{ N}
\]

\[
	F_{\text{total}} \approx -0.0032 \text{ N}
\]

\section{Circular or spiral coil}

\begin{figure}[H]
	\centering
	
	\caption[Simulation the magnetic field in a spiral coil]{Simulation the magnetic field in a spiral coil with 20 turns for a total of 10mm diameter, with a current of 1A}
	\label{fig:simu_spiral}
\end{figure}

We'll take a middle value of 50 uT at around 3mm from the wire.

Given data:
\begin{itemize}
	\item Magnetic flux density of the external field: \( B = 50 \, \mu\text{T} = 50 \times 10^{-6} \text{ T} \)
	\item Magnetic moment: \( m = 2.78 \times 10^{-7} \text{ A} \cdot \text{m}^2 \)
	\item Magnet weight: \( m_{\text{weight}} = 1.6416 \text{ g} = 0.0016416 \text{ kg} \)
	\item Coefficient of friction: \( \mu = 0.2 \)
	\item Acceleration due to gravity: \( g = 9.81 \text{ m/s}^2 \)
	\item Angle between magnetic moment and external field: \( \theta = 90^\circ \), so \( \sin(\theta) = 1 \)
\end{itemize}

Calculate the Magnetic Force

\[
	F_{\text{mag}} = m \cdot B \cdot \sin(\theta)
\]

\[
	F_{\text{mag}} = 2.78 \times 10^{-7} \, \text{A} \cdot \text{m}^2 \times 50 \times 10^{-6} \, \text{T}
\]

\[
	F_{\text{mag}} = 1.39 \times 10^{-10} \text{ N}
\]

Calculate the Friction Force

\[
	F_{\text{friction}} = \mu \cdot m_{\text{weight}} \cdot g
\]

\[
	F_{\text{friction}} = 0.2 \times 0.0016416 \text{ kg} \times 9.81 \text{ m/s}^2
\]

\[
	F_{\text{friction}} \approx 0.0032 \text{ N}
\]

Calculate the Total Force

\[
	F_{\text{total}} = F_{\text{mag}} - F_{\text{friction}}
\]

\[
	F_{\text{total}} = 1.39 \times 10^{-10} \text{ N} - 0.0032 \text{ N}
\]

\[
	F_{\text{total}} \approx -0.0032 \text{ N}
\]

This means that the magnet is too heavy to move from the middle of the coil. We'll have to increase the magnetic field strength to move the magnet.

\section{rectangular coil}

\begin{figure}[H]
	\centering
	
	\caption[Simulation of the magnetic field of a square coil]{Simulation of the magnetic field of a square coil with 15 turns for an area of 8mm x 8mm, with a current of 1A}
	\label{fig:simu_square}
\end{figure}

The forces applied on the magnet seem really weak, i might have issues with my calculations or the friction coefficient. The simulation are not showing what i can really see in real life.

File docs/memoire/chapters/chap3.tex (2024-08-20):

%% Tex spellcheck
% Maybe put this as Chapter 2

% Write in English.
\chapter{Chapter 4 : Testing some coil designs}

We will now test several of the designs discussed in the previous chapter by creating PCBs incorporating these coil designs. Additionally, we will include a driver and control system to regulate the current flowing through the coils.

\section{Existing designs}

To determine the optimal solution for our application, we have tested various existing designs that use PCB coils to move a magnet. For all these tests, we will utilize a driving circuit and a microcontroller mounted on a breadboard.

\subsection{Driver circuit}

In order to control the current in the coils, we will need some driving circuitry. We will use simple NMOS transistors. Leds were added to visually see which coil is activated. The schematics of the driver circuit is shown in figure \ref{fig:breadboard_schematics} and the mounted circuit is shown in figure \ref{fig:breadboard_driver}. Since these coils are inductive, flyback diodes were added to protect the transistors and the power supply.

When setting the GPIOs to a logic high, the transistor will conduct and the current will flow from the power supply to the coil. When setting the GPIOs to a logic low, the transistor will stop conducting.

The same circuit will be used for testing two different existing coil designs.

\begin{figure}[H]
	\centering
	
	\caption[Schematics of the driver breadboard circuit to control the coils]{Schematics of the driver breadboard circuit to control the coils}
	\label{fig:breadboard_schematics}
\end{figure}

\begin{figure}[H]
	\centering
	
	\caption[Mounted Breadboard circuit]{Mounted Breadboard circuit}
	\label{fig:breadboard_driver}
\end{figure}

\subsection{Control firmware}

For this tests, the coils are controlled via a Raspberry Pi PICO\footcite{ltd_buy_nodate} programmed in MicroPython and six \gls{gpio}s are connected to the transistors and will be used to control the current in the coils. The code is shown in figure \ref{fig:up_code}.

\begin{figure}[H]
	\centering
	
	\caption[Micropython code to control the coils with a \gls{pwm}]{Micropython code to control the coils with a \gls{pwm}}
	\label{fig:up_code}
\end{figure}

\subsection{Pemi Technology linear coils}

The first one comes from Pemi Technology\footcite{noauthor_home_nodate} and uses the alternating linear coils. We'll use the driving circuit to control the current in the coils. There is two 4 pin connectors on the \gls{pcb}, one connector for each (X / Y) axis. One of these pins is common to the three coils and will be connected to the power supply, the other three pins are connected to the other side of the coils and will be pulled to ground by transistors to activate the coils.

\begin{figure}[H]
	\centering
	
	\caption[Pemi Technology linear coils \gls{pcb}]{Pemi Technology linear coils \gls{pcb}}
	\label{fig:pemi_pcb}
\end{figure}

The \gls{pcb} characteristics are:
\begin{itemize}
	\item 3 coils for each axis
	\item 10 mils (0.254mm) spacing between each coil
	\item 20 mils (0.508mm) width for the traces
\end{itemize}

The magnet used for the tests:
\begin{itemize}
	\item 3mmx3mmx3mm cubic magnet
	\item 5mmx5mmx5mm cubic magnet
	\item 2mm diamter round magnet
	\item 2mmx2mmx1mm cubic magnet
\end{itemize}

The tests consist on alternating the activation of the coils and see if we could move a magnets. We used different magnet sizes and shapes to see if we could move them.
\\

We could only move the smallest magnets (2mmx2mm) and only in one axis. The direction was managed by the order of activation of the coils, and changing this order did change the diection. There still was some moments where the magnet would be stuck or moving back and forth on the same three coils.
\\

The axis where the magnet was moving was the one on the top layer of the \gls{pcb}, this means that the coils on the bottom layer were not strong enough to move the magnet bacause they were further to the magnet than the top layer ones.

\subsection{HEPIA linear coils}

In a previous intership\footcite{noauthor_arthurabelkalo_2023}, a \gls{pcb} was designed with the same linear coils concept. It's actually compose of 4 identical board, each with 9x9 cell. These cells should be individually controllable to move a magnet in each sub surface. The \gls{pcb} has some issues, notably all the columns are connected together but should be individually controllable. This renders the final \gls{pcb} unusable for our application.\\

Besides the electrical issues, the \gls{pcb} is made on 6 layers with bind vias, making it very hard to develop, expensive to produce and really hard to debug.

\begin{itemize}
	\item 9x9 cell
	\item 6 layer board
	\item Bind vias
	\item 3 coils for each axis
	\item 0.3mm spacing between each coil
	\item 0.5mm width for the traces
\end{itemize}

\begin{figure}[H]
	\centering
	
	\caption[Intern's \gls{pcb} with linear coils]{\gls{hepia} Intern's \gls{pcb} with linear coils}
	\label{fig:intern_pcb}
\end{figure}

\begin{figure}[H]
	\centering
	
	\caption[Single cell intern's \gls{pcb}]{Single cell of the intern's \gls{pcb} with all layers}
	\label{fig:single_cell_all}
\end{figure}

\newpage

\section{Custom PCB to test designs}

In order to test some coil design and to have a better control over the coils while also testing some ways to control the current in the coils, we designed a custom \gls{pcb} with 4 different coil designs. Two of these designs are still linear coils but with different spacing and width. The other two designs are circular coils with different trace width and spacing to see if more turns or more current impacts the magnetic field while keeping the same diameter.

We also wanted to keep the \gls{pcb} as 2 layers to keep the cost down and see if it was enough to move a magnet.

\begin{figure}[H]
	\centering
	
	\caption[Mounted Custom test \gls{pcb} ]{Mounted custom test \gls{pcb}}
	\label{fig:coil_driver_pcb}
\end{figure}

\begin{figure}[H]
	\centering
	
	\caption[Custom test \gls{pcb} general schematics]{Custom test \gls{pcb} general schematics}
	\label{fig:coil_driver_full_schematics}
\end{figure}

\subsection{Driver circuitry}

We would only test one design at the time, so we would only need one driver circuit and we would want to change which coil design is connected to it. For that we simply added pin aligned pin headers so that we can physically connect which design is connected to the driving circuit. One other advantage of this method, is that we can also easily connect any external design on the driving circuit.

\begin{figure}[H]
	\centering
	
	\caption[Pin header for chosing the driven design]{Pin header for chosing the driven design}
	\label{fig:deisgn_choice}
\end{figure}

The driver part is composed of 6 NMOS transistors and some LEDs to visually see which coil is activated.

\begin{figure}[H]
	\centering
	
	\caption[Schematics for transistor part of the custom \gls{pcb}]{Schematics for transistor part of the custom \gls{pcb}}
	\label{fig:transistor_circuit}
\end{figure}

We took advantage of this custom \gls{pcb} to also test a specific transistor to see if it could handle the current in the coils. We used the BUK6D120 NMOS transistor.

It can handle a drain-source voltage of 40 V, and a temperature of 175°C.

We will power the coils with 5V and we can assume that they will be 1 ohm or more. This means that the absolute maximum current that can flow through the coils is 5A. But we will control it with a \gls{pwm} at 20\%, which means that the average current will be 1A.

We now know that we control the Gate of the NMOS with a 3V3 logic \gls{gpio} from the Raspberry Pi PICO. With a Gate Source Voltage of 3V3, we can expect a drain-source resistance of 0.28 ohm as seen in \ref{fig:transistor_rdson}.

\begin{figure}[H]
	\centering
	
	\caption[BUK6D120 NMOS RDSon graph]{BUK6D120 NMOS RDSon graph}
	\label{fig:transistor_rdson}
\end{figure}

This means that the transistor will dissipate

$ P = I^2 * R => 1^2 * 0.28 = 0.28  Watts $

The thermal resistance from junction to ambient is maximum 76°C/W, which means that the temperature rise will be $ 0.28 * 76 = 21.28 $ °C of elevation for a constant current of 1A. This is easily manageable for the transistor.

\subsection{Coil designs}

The choice to have 4 coil designs was made not to have too big of a PCB while still testing different designs.

\subsubsection{Design 1 : Dual Linear coils}

The characteristics of the first design are:

\begin{itemize}
	\item 2 coils for each axis
	\item 10 mils (0.256mm) spacing between each traces
	\item 20 mils (0.508mm) width for the traces
\end{itemize}

\begin{figure}[H]
	\centering
	
	\caption[Dual linear coils design]{Dual linear coils design}
	\label{fig:dual_linear}
\end{figure}

This design is not working as expected. The dual part of the design makes it impossible to have a magnet move in the same direction consitently because the order of the coils does not matter anymore since there is only 2 coils.

\subsubsection{Design 2 : Triple Linear coils}

The characteristics of the second design are:

\begin{itemize}
	\item 3 coils for each axis
	\item 10 mils (0.256mm) spacing between each traces
	\item 20 mils (0.508mm) width for the traces
\end{itemize}

\begin{figure}[H]
	\centering
	
	\caption[Triple linear coils design]{Triple linear coils design}
	\label{fig:triple_linear}
\end{figure}

The design is pretty similar to the Pemi Technology design and is working relatively similar. The main changes have actually been the \gls{pcb} layers since we switched to 4 layers and have routed the traces on the first top ones. Switching to 4 layers changes the stackup so the first 2 layers are closer to the top, thus closer to the magnet. The magnet can move in both direction but is still stuck sometimes. The magnet is moving in the same axis as the top layer of the \gls{pcb}.

\newpage

\subsubsection{Design 3 : Circular coils}

This design is closer to the spiral coil design from Carl Bugeja. The characteristics of this third design are:

\begin{itemize}
	\item 2 layers
	\item 10 mils (0.256mm) trace width
	\item 5 mils (0.128mm) spacing traces
	\item 20mm diameter
	\item 25 turns
\end{itemize}

\begin{figure}[H]
	\centering
	
	\caption[Circular coils design]{Circular coils design}
	\label{fig:circular}
\end{figure}

This was the most promising design since the magnet was beig attracted to the center of the coil from the border of the spiral. But the magnetic field was not strong enough to move a magnet from a coil to the other.

\newpage

\subsubsection{Design 4 : Circular coils with more turns}

This design is quite similar to the third one but with thinner traces and thinner spacing thus making more turns. The characteristics of this fourth design are:

\begin{itemize}
	\item 2 layers
	\item 3.5 mils (0.089mm) trace width
	\item 3.5 mils (0.089mm) spacing traces
	\item 20mm diameter
	\item 50 turns
\end{itemize}

\begin{figure}[H]
	\centering
	
	\caption[Circular coils with more turns]{Circular coils with more turns}
	\label{fig:circular_more_turns}
\end{figure}

This final design should have given us a stronger magnetic for the same current, but with these small traces, the resistance was too high and the current was not enough to move a magnet.

\newpage

\section{Stand alone coil \gls{pcb}s}

These designs were not working perfectly so we went back to the drawing board and got some new designs on smaller \gls{pcb} controlled by the custom board drivers. We only needed to have the designs and some pins to connect to the driver board.
\\

We went for 3 different designs:
\begin{itemize}
	\item 4 layer circular coils to double de strength of the magnetic field of the third previous design
	\item 2x2 layer Circular interlaced coils to have a sub-coil closer between each main coil
	\item 2x2 layer rectangular interlaced coils to have a sub-coil closer between each main coil
\end{itemize}

\subsection{4 Layer circular coils}

This design has the same characteristics as the third previous design but with 4 layers of coil instead of 2. This should almost double the magnetic field strength.

\begin{figure}[H]
	\centering
	
	\caption[4 layer circular coils design]{4 layer circular coils design}
	\label{fig:4_layer_circular}
\end{figure}

\begin{figure}[H]
	\centering
	
	\caption[4 layer circular \gls{pcb}]{4 layer circular \gls{pcb}}
	\label{fig:4_layer_circular_pcb}
\end{figure}

This was not working as expected, the magnet could still not jump from one coil to the other, the doubling of the magnetic field was not enough to move the magnet.

\newpage

\subsection{2x2 layers - Circular interlaced coils}

This design has a small trick to get multiple coils to overlap each other. On the 4 layer stackup we have a coil on the top layer and the inner second layer and the second coil on the first inner layer and the bottom layer. This way, we can have the coils overlapping and it's easier to move the magnet from one coil to the other.

\begin{figure}[H]
	\centering
	
	\caption[\gls{pcb} Stackup 4 layer overlap]{\gls{pcb} Stackup 4 layer overlap}
	\label{fig:stackup_circles}
\end{figure}

One issue with this shape is that it's hard to have them overlap on the 4 sides when being the same diameter, so we had to make smaller coils for the sub-coils. The center of the coils is where the force is the strongest, so we need the center of the coils to be as close as possible from each other.

\begin{figure}[H]
	\centering
	
	\caption[Circular sub coils are smaller]{Circular sub coils are smaller}
	\label{fig:smaller_coils}
\end{figure}

\begin{figure}[H]
	\centering
	
	\caption[Circular sub-coils \gls{pcb}]{Circular sub-coils \gls{pcb}}
	\label{fig:sub_circular_pcb}
\end{figure}

While promising, this design turned out to have it's sub coils too small to be powerfull enough to move a magnets between coils. The issue comes from the circular shapes that are difficult to have them overlap on the 4 sides of the main circle.

\newpage

\subsection{2x2 layers - Rectangular interlaced coils}

This design is similar to the previous one but with rectangular coils. This way we can have the coils overlap on the 4 sides of the main coil while still being the same size as the main.

The stackup is the same, the top layer and the inner second layer have the first coil and the first inner layer and the bottom layer have the second coil.

\begin{figure}[H]
	\centering
	
	\caption[Squares 4 layer overlap]{squares Stackup 4 layer overlap}
	\label{fig:square_design}
\end{figure}

\begin{figure}[H]
	\centering
	
	\caption[Square sub-coils \gls{pcb}]{Square sub-coils \gls{pcb}}
	\label{fig:square_pcb}
\end{figure}

This design was the most promising, I made a 10mm magnet move back and fourth between the coils, it was heating up because the coils were being activated almost all the time, but from what i gathered with the thermal camera, the maximum heating we had was 70°C which is clearly still manageable for the \gls{pcb} and the magnet.

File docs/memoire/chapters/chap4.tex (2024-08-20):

%% Tex spellcheck = fr_FR
\chapter{Chapter 5 : Final Tic-Tac-Toe hardware design}

Now that we found the best coil design, we can make a full matrix of coils to move the magnet in a 2D space. We will use the square coils with sub-coils. we will also need a driver circuit power the matrix of coils individually.

\section{Choice of layout}

We want to make a matrix big enough to play Tic-Tac-Toe. This means that we need at least 3x3 usable cells plus some side coils to hold the non placed pieces. So in the end we need a 5x4 usable matrix of coils. But as we describe in the next section, we also need intermediate buses to avoid attracting the wrong magnets. This means that for each usable cell, we need a triple bus for rows and columns.

\begin{figure}[H]
	\centering
	
	\caption[Description of zones for tic-tac-toe]{Description of zones for tic-tac-toe}
	\label{fig:playable_zones}
\end{figure}

\subsection{Magnet buses}

Since the design can attract magnets from any directions, we need intermediate buses or routes to avoid attracting the wrong magnets.

The issue is a single bus would not be enough since activation a coil on the bus with magnets on both sides would attract both magnets.

\begin{figure}[H]
	\centering
	
	\caption[Magnet single bus]{Magnet single bus}
	\label{fig:single_bus}
\end{figure}

\newpage

A dual bus would still not be enough since when moving from one cell to another, we could come across situations where the path requires to activate a coil on the bus with magnets on both sides.

\begin{figure}[H]
	\centering
	
	\caption[Magnet dual bus]{Magnet dual bus}
	\label{fig:double_bus.png}
\end{figure}

\newpage

The solution would be to have a triple bus system. This way we go onthe middle of the bus to move anywhere without attracting the wrong magnets.

\begin{figure}[H]
	\centering
	
	\caption[Magnet triple bus]{Magnet triple bus}
	\label{fig:triple_bus}
\end{figure}

\begin{figure}[H]
	\centering
	
	\caption[General schematics of final design]{General schematics of final design}
	\label{fig:general_schematics}
\end{figure}

\section{Driver circuit}

Now that we have a matrix of coils, it would take space, time and money to have a driver circuit for each coil. We will use a row and column driving method. This means that each coil will be connected to a row and a column. We will then activate the row and column to activate the coil. This way we can activate any coil in the matrix by activating the corresponding row and column. Each row is driven by a PMOS transistor, pulling one side of the coil to VCC and each column is driven by a NMOS transistor, pulling the other side of the coil to GND.

\begin{figure}[H]
	\centering
	
	\caption[Matrix driving concept]{Matrix driving concept}
	\label{fig:matrix_concept}
\end{figure}

\newpage

This means that each coil is driven by the equivalent of this schematics.

\begin{figure}[H]
	\centering
	
	\caption[Equivalent Dual mos driver circuit]{Equivalent Dual mos driver circuit}
	\label{fig:driver_mos}
\end{figure}

\section{Kicad scripting}

I've tried to leverage the power of scripting in Kicad and create three simple scripts. They need to run with the Kicad's python instance since they use the Kicad API.

\subsection{Footprint generation}
One of them to create the footprint of the coil itself by specifying the parameters of the coils:

\begin{itemize}
	\item The traces width,
	\item The spacing between traces
	\item The side of the square
\end{itemize}

\begin{figure}[H]
	\centering
	
	\caption[Code to generate Kicad square footprint]{Code to generate Kicad square footprint}
	\label{fig:coil_footprint}
\end{figure}

\subsection{Schematic generation}
Now that we have the footprint, we want to generate a matrix of coils in the schematic. For that we need to create a blank schematics and add and configure 2 coils. Then the script will duplicate the coils and connect them to the rows and columns.

\begin{figure}[H]
	\centering
	
	\caption[Code to generate Kicad schematic]{Code to generate Kicad schematic}
	\label{fig:coil_schematic}
\end{figure}

\subsection{PCB generation}

Now that we have the schematic, we want to place the coils in a matrix on the PCBnew software. For that, we need to already have exported the components into PCBnew. We also need text files with the list of names of the coils to position.

\begin{figure}[H]
	\centering
	
	\caption[Code to position coils on the PCB]{Code to position coils on the PCB}
	\label{fig:coil_pcb}
\end{figure}

\newpage

\section{Control}

We will use a microcontroller to control the matrix. We integrated the RP2040 microcontroller from Raspberry Pi on the \gls{pcb}. It has enough GPIOs to control each row and column of the matrix and it can produce at least 16 PWM signals from a dedicated peripheral to control the columns NMOS.

\begin{figure}[H]
	\centering
	
	\caption[RP2040 microcontroller schematics]{RP2040 microcontroller schematics}
	\label{fig:rp2040}
\end{figure}

In order to control bigger matrix, we might have to use a shift reigster to control the rows PMOS, for that purpose, we added a shift register on the \gls{pcb} to future proof the design. Unfortunately, we needed a Serial In Parallel Out shift register with open drain outputs to control the PMOS transistors but I picked the wrong one, so i had to hardwire gpios to the PMOS...

\begin{figure}[H]
	\centering
	
	\caption[Shift register schematics]{Shift register schematics}
	\label{fig:shift_registers}
\end{figure}

\newpage

\begin{figure}[H]
	\centering
	
	\caption[Final Unmounted PCB]{Final Unmounted PCB}
	\label{fig:final_pcb}
\end{figure}

\newpage

The shift registers had to be removed and some gpios were hardwired to the PMOS transistors. We outputed some pads with the remaining free gpios to have some slack in case of issues (Like a wrong Shift register...).

\begin{figure}[H]
	\centering
	
	\caption[Hardware Shift registers fixes]{Hardware Shift registers fixes}
	\label{fig:ugly_hardware_patch}
\end{figure}

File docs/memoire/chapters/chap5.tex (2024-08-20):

\chapter{Chapter 6 : Final Tic-Tac-Toe Software}

For the software component of the Tic-Tac-Toe game, a web application will be used to make the moves. This web app will communicate with a backend system, which will then interface with the microcontroller to control the coils that move the game pieces.

\section{Web App - Frontend}

The web application is straightforward, featuring a 3x3 grid of buttons. When a button is pressed, it sends a request to the backend to execute the move. While the board is making a move, the buttons are temporarily disabled. The web app waits for confirmation from the backend before re-enabling the buttons for the next move.

\begin{figure}[H]
	\centering
	
	\caption[Web app waiting for an acknowledgement after a player move]{Web app waiting for an acknowledgement after a player move}
	\label{fig:web_waiting}
\end{figure}

The web app is made with React.js\footcite{noauthor_react_nodate}, a JavaScript library for building user interfaces. It is a single page application that uses the WebSocket protocol to communicate with the backend.

\section{Web App - Backend}

The backend is a straightforward Python script that establishes a WebSocket connection with the web app. It listens for messages from the web app and forwards them to the microcontroller via serial communication. After receiving an acknowledgment from the microcontroller, the backend sends the result back to the web app.

The serial communication is also simple: the backend sends the move coordinates to the microcontroller, framed by a start byte and a stop byte. Since the frontend handles the game rules and permissions, the backend only receives valid moves, ensuring that no illegal moves are processed.

Packet from the backend to the microcontroller:
\begin{itemize}
	\item Start byte : 0x02
	\item X coordinate : 0 to 2 in ASCII
	\item Y coordinate : 0 to 2 in ASCII
	\item Stop byte : 0x03
\end{itemize}

Packet from the microcontroller to the backend:
\begin{itemize}
	\item Start byte : 0x02
	\item Result : OK or KO in ASCII (KO when issue happened)
	\item Stop byte : 0x03
\end{itemize}

\newpage

\section{Microcontroller firmware}

The RP2040 is programmed in C with the Pico SDK\footcite{noauthor_hardware_nodate} and I decided to use a Real Time Operating System for easier multi task management and timings, I chose FreeRTOS\footcite{noauthor_freertos_nodate}.

The firmware will wait for a packet from the backend, then it will find the best path to move the magnet to the desired position. It will fill a queue with the coils to activate in the correct order. It will then activate the coils one by one and wait some arbitrary time before activating the next coil. When the sequence is done, it will send an acknowledgement to the backend.

The magnets are moved by activating the coils in the correct order. For that, we have to generate a \gls{pwm} signal on the columns and activate the rows.

The RP2040 has an integrated \gls{pwm} peripheral that can be programmed via the Pico SDK API to generate the \gls{pwm} signal.

A simpler API was made to abstract some computing to get the best timer values, so we only have to chose a Frequency and and we can then set a duty cycle from 0.0 to 1.0 when desired.

\begin{figure}[H]
	\centering
	
	\caption[Custom PWM API]{Custom PWM API}
	\label{fig:pwm_api}
\end{figure}

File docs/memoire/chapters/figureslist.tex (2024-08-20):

%% Tex spellcheck = fr_FR
\renewcommand{\listfigurename}{List of Figures}
\listoffigures
\addcontentsline{toc}{chapter}{\listfigurename} % Adding toc entry

\paragraph{URL references}

\begin{itemize}

	\item URL01 \href{https://en.wikipedia.org/wiki/Field\_line\#/media/File:VFPt\_cylindermagnet\_field-representations.svg}{https://en.wikipedia.org/wiki/Field\_line\#/media/File:VFPt\_cylindermagnet\_field-representations.svg}

	\item URL02 \href{https://www.atomic14.com/2022/11/20/simulation-coils.html}{https://www.atomic14.com/2022/11/20/simulation-coils.html}

	\item URL03 \href{https://pcbstator.com/wp-content/uploads/2023/09/Stator-Only-5-e1695660921510-1024x1024.png}{https://pcbstator.com/wp-content/uploads/2023/09/Stator-Only-5-e1695660921510-1024x1024.png}

	\item URL04 \href{https://pcbstator.com/wp-content/uploads/2023/09/thumbnail-1.png}{https://pcbstator.com/wp-content/uploads/2023/09/thumbnail-1.png}

	\item URL05 \href{https://hackaday.io/project/154496-2d-actuator-move-micro-robot-in-xy-2d-space}{https://hackaday.io/project/154496-2d-actuator-move-micro-robot-in-xy-2d-space}

	\item URL06 \href{https://hackaday.io/project/154496/gallery}{https://hackaday.io/project/154496/gallery}

	\item URL07 \href{https://hackaday.io/project/158017-linear-pcb-motor}{https://hackaday.io/project/158017-linear-pcb-motor}

	\item URL07 \href{https://www.youtube.com/watch?v=EJZX66JzVDo}{https://www.youtube.com/watch?v=EJZX66JzVDo}

	\item URL08 \href{https://thumbs.dreamstime.com/b/curl-right-hand-rule-vector-illustration-example-diagram-detecting-direction-induced-current-flow-magnetic-field-physics-173736679.jp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}{https://thumbs.dreamstime.com/b/curl-right-hand-rule-vector-illustration-example-diagram-detecting-direction-induced-current-flow-magnetic-field-physics-173736679.jp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}

	\item URL09 \href{https://www.supermagnete.ch/}{https://www.supermagnete.ch/}

\end{itemize}

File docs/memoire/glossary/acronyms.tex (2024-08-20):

% Acronym definitions

\newacronym{hepia}{HEPIA}{Haute École du Paysage, d'Ingénierie et d'Architecture de Genève}
\newacronym{usa}{USA}{United States of America}

\newacronym{fpga}{FPGA}{Field Programmable Gate Array}
\newacronym{pcb}{PCB}{Printed Circuit Board}
\newacronym{pwm}{PWM}{Pulse Width Modulation}
\newacronym{gpio}{GPIO}{General Purpose Input Output}

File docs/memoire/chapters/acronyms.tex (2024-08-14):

%% Tex spellcheck = fr_FR
\printnoidxglossary[type=\acronymtype,title={Glossary}]

%% Use the acronyms
%\vspace{5cm}
%\textit{NB : Vous pouvez utiliser des acronymes en les définissant dans le fichier externe \texttt{/glossary/acronyms}. Une page dans la table des matières sera automatiquement ajoutée. Vous pourrez ensuite les référencer dans votre texte comme dans l'exemple ci-après:}\medskip

%\gls{utc} is 3 hours behind \gls{adt} and 10 hours ahead of \gls{est}.\medskip

%\textit{Lors de la première déclaration, l'acronyme est accompagné de sa définition, mais lors des utilisations suivantes, il ne l'est plus, comme illustré ci-dessous:}\medskip

%\gls{utc} is 3 hours behind \gls{adt} and 10 hours ahead of \gls{est}.

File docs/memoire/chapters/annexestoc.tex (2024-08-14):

%% Tex spellcheck = fr_FR
\chapter*{List of appendices} % No (numbered) toc entry with *
\addcontentsline{toc}{chapter}{Liste des annexes} % Adding toc entry

\printcontents[annexes]{ }{2}{}

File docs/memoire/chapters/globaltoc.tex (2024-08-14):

%% Tex spellcheck = fr_FR
\chapter*{Table Of Contents}

\startcontents[default]
\printcontents[default]{ }{1}{}

\startcontents[annexes]
\stopcontents[annexes]

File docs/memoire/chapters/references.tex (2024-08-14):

%% Tex spellcheck = fr_FR
\chapter*{Bibliography}
\addcontentsline{toc}{chapter}{Bibliography} % Adding toc entry

\nocite{*}
\printbibliography[heading=none, omitnumbers=true]
%\printbibliography[heading=none]
%\printbibliography[]

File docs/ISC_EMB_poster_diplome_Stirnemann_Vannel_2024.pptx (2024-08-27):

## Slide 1

- Plateforme de traitement d'image sur FPGA via PCI Express


Nicolas ALBANESI

- Contexte / Objectifs
- L'entreprise Elix Systems a développé le Summit-X, un ordinateur de bord destiné à l'avionique permettant de faire du switching vidéo entre quatre entrées et quatre sorties SDI. Les vidéos acquises par un FPGA sont transmises à un CPU pour faire du traitement sur la vidéo, puis réinjectées dans le FPGA via une interface HDMI. L'utilisation de cette interface HDMI ajoute de la latence au système et limite la résolution maximale des vidéos. L'objectif du projet est de modifier le Summit-X en réinjectant la vidéo via le bus PCIe sans utiliser de mémoire DDR, afin de réduire la latence et d’augmenter la résolution maximale.


Summit-X avant modification


Summit-X après modification

- Conclusion
- La transmission de 12 flux en simultané a été réalisé avec succès en utilisant une carte de développement. Le projet a également pu être intégré dans le Summit-X pour un flux vidéo.

- Réalisations Techniques
- La première phase du projet était une phase de recherche / expérimentation. Durant cette phase, des mesures de vitesses de transfert du bus PCIe ont été effectuées afin de décider si de simples accès mémoire étaient possible ou si l'utilisation d'un DMA était indispensable. L'utilisation d'un DMA étant nécessaire, un DMA spécifique pour le transfert de vidéo a été choisi (VDMA). La seconde phase du projet était une phase de design. Durant celle-ci, un design utilisant un DMA a été réalisé dans le FPGA, ainsi qu'un driver Linux afin de communiquer avec ce DMA. Le framework Video4Linux2 a été intégré au driver afin d'obtenir une interface standardisée et facile à utiliser. La réalisation du driver s'est faite de manière à faciliter l'intégration avec le driver présent dans le Summit-X réalisé par Elix Systems.


- Sous la direction de Messieurs Laurent GANTEL et Andrés UPEGUI
- En collaboration avec Elix Systems SA

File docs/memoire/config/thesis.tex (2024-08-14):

%%%%%%%%%%%%%%%%%%%%%%%%%%%%%%%%%%%%%%%%%%%%%%%%%%%%%%%%%%%%%%%%%%%%%%%%%%%%%%%%
%%                                                                             %
%% HEPIA BACHELOR THESIS LATEX TEMPLATE                                        %
%% version 0.10 - 2020/04/25                                                    %
%%                                                                             %
%%%%%%%%%%%%%%%%%%%%%%%%%%%%%%%%%%%%%%%%%%%%%%%%%%%%%%%%%%%%%%%%%%%%%%%%%%%%%%%%
%\documentclass[12pt]{report}
\usepackage[T1]{fontenc}
\usepackage[utf8]{inputenc}
%\usepackage[french]{babel}
\usepackage[cm]
			{fullpage}	% Set margins to full page
\usepackage[a4paper,includeheadfoot,margin=2.5cm]{geometry}
%\usepackage[a4paper,includehead,includefoot,top=2.1cm,bottom=2.5cm,right=2.5cm,left=2.5cm]{geometry}
\usepackage{lmodern}	% latin Modern font (FALLBACK FONT)

\usepackage{caption}
\captionsetup{labelfont=sc}
% You can change names of table and figure here
\def\frenchtablename{Tableau} 

\def\frenchfigurename{Illustration} 

\usepackage{float}
\usepackage{tikz}		% Image and drawing related package - TITLE PAGE
\usepackage{setspace}	% Custom spacing package            - TITLE PAGE
\usepackage{array}		% Array related package				- TITLE PAGE
\usepackage{helvet}		% Helvetica font ~ Arial			- TITLE PAGE
\usepackage{mathptmx}	% Times font ~ Times New Roman
\usepackage{carlito}	% Calibri replacement font
\usepackage[scaled=0.85]
			{beramono}	% Vera mononspace {fvm}

%% This defines the default sans serif, roman and monospace fonts
\renewcommand{\sfdefault}{phv}	% helvetica as sans serif font
\renewcommand{\rmdefault}{ptm}	% times as roman (serif) font
\renewcommand{\ttdefault}{fvm}	% Vera mononspace as monospace font
\usepackage{bold-extra}	% Allow custom typsettings horrors like bold Small Caps
\usepackage{slantsc}	% Allow custom typsettings horrors like bold Small Caps

\usepackage[bigcaptions]
			{listing}	% listing related package
\usepackage{listings}	% listing related package
\usepackage{titletoc}
%\usepackage{tocbibind}	% TOC related package
\usepackage[titles]
			{tocloft}	% TOC related package - here to add dots to chapter leader in TOC
\renewcommand{\cftchapleader}{\cftdotfill{\cftdotsep}}
\usepackage{lipsum}		% Lorem Ipsum generator

\usepackage{fancyhdr}
\usepackage{graphicx}	
\usepackage{color}
\usepackage{xcolor}
\usepackage{chngcntr}	% counter related package
%\usepackage{emptypage}	% adds blank pages without number, but keeps page numbering going on

\graphicspath{{figures/}}

\usepackage[acronym,toc,shortcuts,hyperfirst=true]{glossaries}
\makenoidxglossaries
\input{glossary/acronyms}
\glsenablehyper
\renewcommand*{\glstextformat}[1]{\textcolor{darkblue}{#1}}

\usepackage[htt]
			{hyphenat}	% hyphenation related package
\usepackage[hyperfootnotes=true,
			linkcolor=darkgray,
			citecolor=black,
			filecolor=black,
			pagecolor=black,
			urlcolor=darkblue,
			linktoc=all,
			bookmarks=true,
			pdfborder={0 0 0},
			pdfdisplaydoctitle=true,
			pdftoolbar=true,
			pdfmenubar=true,
			pdfstartview=X Y Z,
			pdfstartpage=1,
			breaklinks]
			{hyperref}	% URL and hyperlinks configuration, with hard break if too long lines
			
\usepackage[hyphens]{url}
\sloppy % helps with url hyphenation if we no not use xurl.
%% IF YOUR URLS LOOK UGLY AND WAY TO LONG, UNCOMMENT THE LINE BELOW AND __DO NOT__ USE OVERLEAF, WHICH DOESN'T SUPPORT EXTENDED LATEX PACKAGES
%\usepackage{xurl}
\usepackage{numprint}	% number notation related package, e.g 10'000'000
%\usepackage{amsmath}	% math related package

\counterwithout{footnote}{chapter}

\usepackage{setspace}	% linespacing related package

\definecolor{codebg}{rgb}{0.98,0.98,0.98}
\definecolor{sectcol}{rgb}{0.094,0.184,0.486}
\definecolor{darkgray}{rgb}{0.2,0.2,0.2}
\definecolor{darkblue}{rgb}{0.2,0.2,0.4}

%%%%%%%%%%%%%%%%%%%%%%%%%%%%%%%%%%%%%% CUSTOM TOC %%%%%%%%%%%%%%%%%%%%%%%%%%%%%%%%%
%% This defines the way section and subsections are numbered.
%% Uncomment to have section numbered without chapter number
% \renewcommand\thesection{\arabic{section}}
% having subsections numbered with letters
\renewcommand{\thesubsection}{\alph{subsection}}

%% This allows you to tweak the depth numbering of the TOC and the sections
\setcounter{tocdepth}{3}	% TOC depth numbering set to 3
\setcounter{secnumdepth}{3}	% section depth numbering set to 3
%%%%%%%%%%%%%%%%%%%%%%%%%%%%%%%%%%%%% /CUSTOM TOC %%%%%%%%%%%%%%%%%%%%%%%%%%%%%%%%%

%%%%%%%%%%%%%%%%%%%%%%%%%%%%%%%% CUSTOM CHAPTER TITLES %%%%%%%%%%%%%%%%%%%%%%%%%%%%
\usepackage{titlesec}
\titleformat{\chapter}[hang]{\fontsize{15.5}{18.7}\centering\bfseries\scshape}{}{1pc}{}
\titleformat{name=\chapter,numberless}[hang]{\fontsize{15.5}{18.7}\centering \selectfont \bfseries\scshape}{}{1pc}{}
\titlespacing{\chapter}{0pc}{-0.44cm}{0.64cm}
\titleformat{\section}[hang] {\fontsize{13.5}{16.7}\bfseries\scshape}{\thesection.}{1pc}{}[]
\titlespacing{\section}{0pc}{6pt}{5pt}
\titleformat{\subsection}[hang] {\bfseries\large}{\hspace*{1em} \thesubsection.}{1pc}{}
\titlespacing{\subsection}{0pc}{4pt}{15pt}
\titleformat{\subsubsection}[hang] {\bfseries\large}{\hspace*{2em} \thesubsubsection.}{1pc}{}
%%%%%%%%%%%%%%%%%%%%%%%%%%%%%%% /CUSTOM CHAPTER TITLES %%%%%%%%%%%%%%%%%%%%%%%%%%%%

\author{\Author}
\title{\Title}

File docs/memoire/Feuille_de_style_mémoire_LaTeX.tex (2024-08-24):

%% TeX spellcheck = fr_FR
%%%%%%%%%%%%%%%%%%%%%%%%%%%%%%%%%%%%%%%%%%%%%%%%%%%%%%%%%%%%%%%%%%%%%%%%%%%%%%%%
%%                                                                             %
%% HEPIA BACHELOR THESIS LATEX TEMPLATE                                        %
%% version 0.10 - 2020/04/22                                                    %
%%                                                                             %
%%%%%%%%%%%%%%%%%%%%%%%%%%%%%%%%%%%%%%%%%%%%%%%%%%%%%%%%%%%%%%%%%%%%%%%%%%%%%%%%
\RequirePackage[hyphens]{url}

\documentclass[12pt
%% UNCOMMENT THE LINE BELOW TO HAVE CHAPTER STARTING ON THE RIGHT PAGE
%			,twoside, openright
			]{report} %% should use memoir documentclass

\usepackage[style=verbose]{biblatex}
\addbibresource{sources.bib}

\input{config/thesis}

\usepackage{anyfontsize}
\usepackage{pdfpages}

%% To fill up by the student
\newcommand{\Author}{Jonas STIRNEMANN}
\newcommand{\TitleImage}{figures/front.png}
\newcommand{\Title}{Magnetic Tic-Tac-Toe}
\newcommand{\Shorttitle}{Magnetic Tic-Tac-Toe}
\newcommand{\Orientation}{Embedded systems}
\newcommand{\Professor}{Fabien Vannel}
\newcommand{\Client}{HEPIA}
\newcommand{\Year}{2024}
\newcommand{\Month}{September}
%% THE LINES BELLOW ARE FOR PDF REFERENCING PURPOSES.
\newcommand{\Keywords}{Magnetic, Tic-Tac-Toe, Embedded systems}
\newcommand{\Subject}{Magnetic Tic-Tac-Toe}
\newcommand{\Convention}{No}
\newcommand{\Confidentiel}{No}

%% DO NOT MODIFY \hypersetup BELOW. THIS IS FOR PDF REFERENCING PURPOSES.
\hypersetup{
	pdftitle={\Title},
	pdfauthor={\Author},
	pdfkeywords={\Keywords},
	pdfsubject={\Subject}
}
%\usepackage{showframe}	% Prints document frame

\input{template/header}

%%%%%%%%%%%%%%%%%%%%%%%%%%%%%%%%%%%%%%%%%%%%%%%%%%%%%%%%%%%%%%%%%%%%%%%%%%%%%%%%
%%%%%%%%%%%%%%%%%%%%%%%%%%%%%%%% DOCUMENT STARTS BELOW %%%%%%%%%%%%%%%%%%%%%%%%%
%%%%%%%%%%%%%%%%%%%%%%%%%%%%%%%%%%%%%%%%%%%%%%%%%%%%%%%%%%%%%%%%%%%%%%%%%%%%%%%%
\begin{document}
\pagenumbering{roman}
%%%%%%%%%%%%%%%%%%%%%%%%%%%%%%%%%%%%%%%% TITLE %%%%%%%%%%%%%%%%%%%%%%%%%%%%%%%%%
\input{template/title}
%\clearpage
\cleardoublepage
%%%%%%%%%%%%%%%%%%%%%%%%%%%%%%%%%%% IMAGE TITLE REF %%%%%%%%%%%%%%%%%%%%%%%%%%%%
%\newgeometry{top=2.1cm,bottom=3.5cm,right=2.5cm,left=2.5cm}
%\begin{spacing}{1.5}
%	\input{chapters/titleref}
%\end{spacing}
%%\clearpage
%\cleardoublepage
%%%%%%%%%%%%%%%%%%%%%%%%%%%%%%%%%%%%%% DEDICATION %%%%%%%%%%%%%%%%%%%%%%%%%%%%%%
%%%%%%%%%%%%%%%%%%%%%%%%%%%%%%%%%%% TABLE OF CONTENT %%%%%%%%%%%%%%%%%%%%%%%%%%%
\begin{spacing}{1}
	\input{chapters/globaltoc}
\end{spacing}
%\clearpage
\cleardoublepage
%%%%%%%%%%%%%%%%%%%%%%%%%%%%%%%%%%%%%% DEDICATION %%%%%%%%%%%%%%%%%%%%%%%%%%%%%%
\begin{spacing}{1.5}
	%\input{chapters/dedication}
	%\clearpage
	%\cleardoublepage
	\includepdf[pages=-]{figures/enonce.pdf}
	%%%%%%%%%%%%%%%%%%%%%%%%%%%%%%%%%%% ACKNOWLEDGEMENTS %%%%%%%%%%%%%%%%%%%%%%%%%%%
	%\input{chapters/acknowledgements}
	%\clearpage
	%\cleardoublepage
	%%%%%%%%%%%%%%%%%%%%%%%%%%%%%%%%%%%%%%% ABSTRACT %%%%%%%%%%%%%%%%%%%%%%%%%%%%%%%
	\input{chapters/abstract}
	%\clearpage
	\cleardoublepage
	%%%%%%%%%%%%%%%%%%%%%%%%%%%%%%%%%%% LIST OF ACRONYMS  %%%%%%%%%%%%%%%%%%%%%%%%%%
	\input{chapters/acronyms}
	%\clearpage
	\cleardoublepage
	%%%%%%%%%%%%%%%%%%%%%%%%%%%%%%%%%%% LIST OF FIGURES %%%%%%%%%%%%%%%%%%%%%%%%%%%%
	\input{chapters/figureslist}
	%\clearpage
	\cleardoublepage
	%%%%%%%%%%%%%%%%%%%%%%%%%%%%%%%%%%%% LIST OF TABLES %%%%%%%%%%%%%%%%%%%%%%%%%%%%
	%\input{chapters/tableslist}
\end{spacing}
%\clearpage
\cleardoublepage
%%%%%%%%%%%%%%%%%%%%%%%%%%%%%%%%%%% LIST OF ANNEXES %%%%%%%%%%%%%%%%%%%%%%%%%%%%
%%% COMMENT THIS PART IF YOU DO NOT USE DEDICATED TOC FOR ANNEXES AND COMMENT 
%%% HEADER AND FOOTER PART IN {chapters/annexes} FILE
\begin{spacing}{1}
	\input{chapters/annexestoc}
\end{spacing}
%\clearpage
\cleardoublepage
%%%%%%%%%%%%%%%%%%%%%%%%%%%%%%%%%%%%% INTRODUCTION  %%%%%%%%%%%%%%%%%%%%%%%%%%%%
\begin{spacing}{1.5}
	\pagenumbering{arabic}
	\input{chapters/intro}
	%\clearpage
	\cleardoublepage
	%%%%%%%%%%%%%%%%%%%%%%%%%%%%%%%%%%%%%%% CHAPTERS %%%%%%%%%%%%%%%%%%%%%%%%%%%%%%%
	%%%%%%%%%%%%%%%%%%%%%%%%%%%%%%% Add your chapters here %%%%%%%%%%%%%%%%%%%%%%%%%
	%\input{chapters/chapXXX}
	\input{chapters/chap0}
	\input{chapters/chap1}
	\input{chapters/chap2}
	\input{chapters/chap3}
	\input{chapters/chap4}
	\input{chapters/chap5}
	\input{chapters/conclusion}
	\input{chapters/annexes}
	\input{chapters/references}
\end{spacing}
\end{document}
%%%%%%%%%%%%%%%%%%%%%%%%%%%%%%%%%% DOCUMENT ENDS HERE %%%%%%%%%%%%%%%%%%%%%%%%%%

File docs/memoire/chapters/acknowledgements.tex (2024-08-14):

%% Tex spellcheck = fr_FR
\chapter*{Remerciements} % No (numbered) toc entry with *
\addcontentsline{toc}{chapter}{Remerciements} % Adding toc entry

\textit{< Formulez ici vos remerciements aux personnes qui vous ont aidé dans la réalisation de votre travail. >}

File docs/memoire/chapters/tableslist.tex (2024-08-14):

%% Tex spellcheck = fr_FR
\renewcommand{\listtablename}{Liste des tableaux}
\listoftables
\addcontentsline{toc}{chapter}{\listtablename} % Adding toc entry

\vspace*{14.4pt}

\textit{N.B. Si vous avez peu de tableaux, vous pouvez les intégrer à la table des illustrations.}

\vspace*{14.4pt}

\paragraph{Références des URL}

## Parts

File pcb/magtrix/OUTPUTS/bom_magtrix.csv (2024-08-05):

U1 | W25Q128JVS | W25Q128JVSIM | 454-W25Q128JVSIM | Package_SO:SOIC-8_5.23x5.23mm_P1.27mm | 1
U3 | RP2040 | SC0914(13) | 358-SC091413 | Package_DFN_QFN:QFN-56-1EP_7x7mm_P0.4mm_EP3.2x3.2mm | 1
U4 | AMS1117-3.3 | LM1117MPX-3.3/NOPB | 926-LM1117MPX3.3NOPB | Package_TO_SOT_SMD:SOT-223-3_TabPin2 | 1
Y1 | 12Mhz | 830069944 | 710-830069944 | CRYSTAL:crystal | 1
C6,C7 | 20p | CL10C200JB8NNNC | 187-CL10C200JB8NNNC | Capacitor_SMD:C_0603_1608Metric | 2
C10,C11 | 1u | CL10A105KA8NNNC | 187-CL10A105KA8NNNC | Capacitor_SMD:C_0603_1608Metric | 2
C18,C19 | 10u | CL31A106MBHNNNE | 187-CL31A106MBHNNNE | Capacitor_SMD:C_1206_3216Metric | 2
IC1,IC2 | SN74HCS16507DR | SN74HCS16507DR | 595-SN74HCS16507DR | SOIC127P600X175-16N | 2
R33,R35 | 10k | CRCW060310K0JNEC | 71-CRCW060310K0JNEC | Resistor_SMD:R_0603_1608Metric | 2
R37,R38 | 33 | CRCW060333R0JNEA | 71-CRCW0603J-33-E3 | Resistor_SMD:R_0603_1608Metric | 2
R39,R40 | 5k1 | CR0603AFX-5101EAS | 652-CR0603AFX5101EAS | Resistor_SMD:R_0603_1608Metric | 2
SW1,SW2 | SW_MEC_5E | PTS526 SM15 SMTR2 LFS | 611-PTS526SM15SMTR2L | push_button:TS-1187A-B-A-B | 2
C3,C8,C9,C12,C13,C14,C15,C16,C17 | 100n | TMK107BJ104KA-T | 963-TMK107BJ104KA-T | Capacitor_SMD:C_0603_1608Metric | 9
C1,C2,C4,C5,C20,C21,C22,C23,C24,C25,C26,C27,C28 | 100u | VZL101M1ETR-0607 | 140-VZL101M1ETR-0607 | BULK:CAPAE660X800N | 13
Q17,Q18,Q19,Q20,Q21,Q22,Q23,Q24,Q25,Q26,Q27,Q28,Q29 | BUK6D120-60PX | BUK6D120-60PX | 771-BUK6D120-60PX | TRANSISTOR_PMOS:BUK6D12060PX | 13
D1,D3,D4,D5,D6,D7,D8,D9,D10,D11,D12,D13,D14,D18,D19,D20,D21,D22,D23,D24,D25,D26,D27,D28,D29,D30 | LED_Small_Filled | 599-0210-007F | 645-599-0210-007F | LED_SMD:LED_1206_3216Metric | 26
R2,R4,R6,R8,R10,R12,R14,R16,R18,R20,R22,R24,R26,R42,R44,R46,R48,R50,R52,R54,R56,R58,R60,R62,R64,R66 | 120k | RCV1206120KFKEA | 71-RCV1206120KFKEA | Resistor_SMD:R_1206_3216Metric | 26
R1,R3,R5,R7,R9,R11,R13,R15,R17,R19,R21,R23,R25,R34,R36,R41,R43,R45,R47,R49,R51,R53,R55,R57,R59,R61,R63,R65 | 1k | ERJ-S08F1001V | 667-ERJ-S08F1001V | Resistor_SMD:R_1206_3216Metric | 28
D2,D15,D16,D17,D31,D32,D33,D34,D35,D36,D37,D38,D39,D40,D41,D42,D43,D44,D45,D46,D47,D48,D49,D50,D51,D52,D53,D54,D55,D56,D57,D58,D59,D60,D61,D62,D63,D64,D65,D66,D67,D68,D69,D70,D71,D72,D73,D74,D75,D76,D77,D78,D79,D80,D81,D82,D83,D84,D85,D86,D87,D88,D89,D90,D91,D92,D93,D94,D95,D96,D97,D98,D99,D100,D101,D102,D103,D104,D105,D106,D107,D108,D109,D110,D111,D112,D113,D114,D115,D116,D117,D118,D119,D120,D121,D122,D123,D124,D125,D126,D127,D128,D129,D130,D131,D132,D133,D134,D135,D136,D137,D138,D139,D140,D141,D142,D143,D144,D145,D146,D147,D148,D149,D150,D151,D152,D153,D154,D155,D156,D157,D158,D159 | CUS05S30 | CUS05S30,H3F | 757-CUS05S30H3F | FLYBACK:CUS05S30H3F | 133
Q1,Q2,Q3,Q4,Q5,Q6,Q7,Q8,Q9,Q10,Q11,Q12,Q13 | BUK6D120 | BUK6D120-40EX | 771-BUK6D120-40EX | TRANSISTOR_NMOS:TRANS_BUK9D23-40EX | 13
USB1 | ~ |  |  | USBC:USBC_16P | 1
J1 | Conn_01x08_Pin |  |  | Connector_PinHeader_1.00mm:PinHeader_1x08_P1.00mm_Vertical_SMD_Pin1Left | 1
J2,J3 | Conn_01x03_Pin |  |  | Connector_PinHeader_2.54mm:PinHeader_1x03_P2.54mm_Vertical | 2

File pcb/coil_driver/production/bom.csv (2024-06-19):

Designator | Footprint | Quantity | Value | LCSC Part #
C1, C2, C3, C4, C5, C6, C7 | 1206 | 7 | 10u
D1, D10, D13, D16, D2, D7 | 1206 | 6 | LED_Small_Filled
D12, D15, D18, D4, D6, D9 | D_SOD-128 | 6 | D_Small
J1, J10, J11, J12, J2, J3, J4, J5, J6, J7, J8, J9 | PinHeader_1x04_P2.54mm_Vertical | 12 | Conn_01x04_Pin
J13, J14 | PinHeader_1x03_P2.54mm_Vertical | 2 | Conn_01x03_Pin
L1, L2, L3, L4, L5, L6 | rounded_thin | 6 | rounded_coil
L10, L11, L12, L7, L8, L9 | rounded_thicc | 6 | rounded_coil
Q1, Q2, Q3, Q4, Q5, Q6 | TRANS_BUK9D23-40EX_3Dadded | 6 | BUK6D120
R1, R10, R13, R16, R3, R6 | 1206 | 6 | 1k
R12, R15, R18, R2, R5, R8 | 1206 | 6 | 120k
TP1, TP10, TP11, TP12, TP13, TP14, TP15, TP16, TP17, TP18, TP19, TP2, TP20, TP3, TP4, TP5, TP6, TP7, TP8, TP9 | pad_dual | 20 | TestPoint_2Pole
U2 | RPi_Pico_SMD_TH | 1 | Pico

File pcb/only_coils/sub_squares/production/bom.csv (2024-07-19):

Designator | Footprint | Quantity | Value | LCSC Part #
J2 | PinHeader_1x06_P2.54mm_Vertical | 1 | Conn_01x06_Pin
J4 | PinHeader_1x03_P2.54mm_Vertical | 1 | Conn_01x03_Pin
L1, L4, L5 | top_coil | 3 | top_coil
L2, L3, L6 | sub_coil | 3 | sub_coil

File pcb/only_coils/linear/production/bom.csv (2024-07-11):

Designator | Footprint | Quantity | Value | LCSC Part #
J3 | PinHeader_1x06_P2.54mm_Vertical | 1 | Conn_01x06_Pin
J4 | PinHeader_1x03_P2.54mm_Vertical | 1 | Conn_01x03_Pin
TP1, TP10, TP11, TP12, TP2, TP3, TP4, TP5, TP6, TP7, TP8, TP9 | pads_dual | 12 | TestPoint_2Pole

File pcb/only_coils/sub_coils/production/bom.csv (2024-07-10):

Designator | Footprint | Quantity | Value | LCSC Part #
J2 | PinHeader_1x06_P2.54mm_Vertical | 1 | Conn_01x06_Pin
J4 | PinHeader_1x03_P2.54mm_Vertical | 1 | Conn_01x03_Pin
L1, L3, L4 | sub_coil_small_2 | 3 | sub_coil
L2, L5, L7 | top_coil | 3 | top_coil

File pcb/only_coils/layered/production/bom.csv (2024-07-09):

Designator | Footprint | Quantity | Value | LCSC Part #
J2 | PinHeader_1x06_P2.54mm_Vertical | 1 | Conn_01x06_Pin
J4 | PinHeader_1x03_P2.54mm_Vertical | 1 | Conn_01x03_Pin
L10, L11, L12, L7, L8, L9 | 4layer_coil | 6 | coil_4_layers

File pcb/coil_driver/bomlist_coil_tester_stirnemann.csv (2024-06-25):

Reference | Value | Qty | MFR | MOUSER
C1,C2,C3,C4,C5,C6,C7 | 10u | 7 | CL31A106MBHNNNE | 187-CL31A106MBHNNNE
D1,D2,D7,D10,D13,D16 | LED_Small_Filled | 6 | 599-0210-007F | 645-599-0210-007F
D4,D6,D9,D12,D15,D18 | D_Small | 6 | YQ3LAM10DTR | 755-YQ3LAM10DTR
J1,J2,J3,J4,J5,J6,J7,J8,J9,J10,J11,J12 | Conn_01x04_Pin | 12 | 826629-4 | 571-826629-4
J13,J14 | Conn_01x03_Pin | 2 | 826629-4 | 571-826629-4
R1,R3,R6,R10,R13,R16 | 1k | 6 | ERJ-S08F1001V | 667-ERJ-S08F1001V
R2,R5,R8,R12,R15,R18 | 120k | 6 | RCV1206120KFKEA | 71-RCV1206120KFKEA
U2 | Pico | 1 | SC0915 | 358-SC0915

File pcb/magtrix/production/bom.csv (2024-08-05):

Designator | Footprint | Quantity | Value | LCSC Part #
C1, C2, C20, C21, C22, C23, C24, C25, C26, C27, C28, C4, C5 | CAPAE660X800N | 13 | 100u
C10, C11 | 0603 | 2 | 1u | C15849
C12, C13, C14, C15, C16, C17, C3, C8, C9 | 0603 | 9 | 100n | C14663
C18, C19 | 1206 | 2 | 10u | C96446
C6, C7 | 0603 | 2 | 20p | C1658
D1, D10, D11, D12, D13, D14, D18, D19, D20, D21, D22, D23, D24, D25, D26, D27, D28, D29, D3, D30, D4, D5, D6, D7, D8, D9 | 1206 | 26 | LED_Small_Filled
D100, D101, D102, D103, D104, D105, D106, D107, D108, D109, D110, D111, D112, D113, D114, D115, D116, D117, D118, D119, D120, D121, D122, D123, D124, D125, D126, D127, D128, D129, D130, D131, D132, D133, D134, D135, D136, D137, D138, D139, D140, D141, D142, D143, D144, D145, D146, D147, D148, D149, D15, D150, D151, D152, D153, D154, D155, D156, D157, D158, D159, D16, D17, D2, D31, D32, D33, D34, D35, D36, D37, D38, D39, D40, D41, D42, D43, D44, D45, D46, D47, D48, D49, D50, D51, D52, D53, D54, D55, D56, D57, D58, D59, D60, D61, D62, D63, D64, D65, D66, D67, D68, D69, D70, D71, D72, D73, D74, D75, D76, D77, D78, D79, D80, D81, D82, D83, D84, D85, D86, D87, D88, D89, D90, D91, D92, D93, D94, D95, D96, D97, D98, D99 | CUS05S30H3F | 133 | CUS05S30
IC1, IC2 | SOIC127P600X175-16N | 2 | SN74HCS16507DR
J1 | PinHeader_1x08_P1.00mm_Vertical_SMD_Pin1Left | 1 | Conn_01x08_Pin
J2, J3 | PinHeader_1x03_P2.54mm_Vertical | 2 | Conn_01x03_Pin
Q1, Q10, Q11, Q12, Q13, Q2, Q3, Q4, Q5, Q6, Q7, Q8, Q9 | TRANS_BUK9D23-40EX | 13 | BUK6D120
Q17, Q18, Q19, Q20, Q21, Q22, Q23, Q24, Q25, Q26, Q27, Q28, Q29 | BUK6D12060PX | 13 | BUK6D120-60PX
R1, R11, R13, R15, R17, R19, R21, R23, R25, R3, R41, R43, R45, R47, R49, R5, R51, R53, R55, R57, R59, R61, R63, R65, R7, R9 | 1206 | 26 | 1k
R10, R12, R14, R16, R18, R2, R20, R22, R24, R26, R4, R42, R44, R46, R48, R50, R52, R54, R56, R58, R6, R60, R62, R64, R66, R8 | 1206 | 26 | 120k
R33, R35 | 0603 | 2 | 10k | C25804
R34, R36 | 1206 | 2 | 1k | C21190
R37, R38 | 0603 | 2 | 33 | C23140
R39, R40 | 0603 | 2 | 5k1 | C23186
SUB1, SUB10, SUB100, SUB101, SUB102, SUB11, SUB12, SUB13, SUB14, SUB15, SUB17, SUB18, SUB19, SUB2, SUB20, SUB21, SUB22, SUB25, SUB26, SUB27, SUB28, SUB29, SUB3, SUB30, SUB31, SUB33, SUB34, SUB35, SUB36, SUB37, SUB38, SUB4, SUB41, SUB42, SUB43, SUB44, SUB45, SUB46, SUB47, SUB49, SUB5, SUB50, SUB51, SUB52, SUB53, SUB54, SUB57, SUB58, SUB59, SUB6, SUB60, SUB61, SUB62, SUB63, SUB65, SUB66, SUB67, SUB68, SUB69, SUB70, SUB73, SUB74, SUB75, SUB76, SUB77, SUB78, SUB79, SUB81, SUB82, SUB83, SUB84, SUB85, SUB86, SUB89, SUB9, SUB90, SUB91, SUB92, SUB93, SUB94, SUB95, SUB97, SUB98, SUB99 | sub_coil | 84 | sub_coil
SW1, SW2 | TS-1187A-B-A-B | 2 | SW_MEC_5E
TOP1, TOP10, TOP11, TOP12, TOP13, TOP14, TOP15, TOP17, TOP18, TOP19, TOP2, TOP20, TOP21, TOP22, TOP23, TOP25, TOP26, TOP27, TOP28, TOP29, TOP3, TOP30, TOP31, TOP33, TOP34, TOP35, TOP36, TOP37, TOP38, TOP39, TOP4, TOP41, TOP42, TOP43, TOP44, TOP45, TOP46, TOP47, TOP49, TOP5, TOP50, TOP51, TOP52, TOP53, TOP54, TOP55, TOP6, TOP7, TOP9 | top_coil | 49 | top_coil
U1 | SOIC-8_5.23x5.23mm_P1.27mm | 1 | W25Q128JVS | C97521
U3 | QFN-56-1EP_7x7mm_P0.4mm_EP3.2x3.2mm | 1 | RP2040 | C2040
U4 | SOT-223-3_TabPin2 | 1 | AMS1117-3.3 | C173386
USB1 | USBC_16P | 1 | ~ | C2765186
Y1 | crystal | 1 | 12Mhz | C9002

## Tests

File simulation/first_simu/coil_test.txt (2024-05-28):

1.5076679,0.0838888,0,1
1.507144366109452,0.08363326068687559,0,1
1.5066313002518792,0.08335730507287639,0,1
1.5061294982138198,0.08306136117666607,0,1
1.5056397383111586,0.0827458880195675,0,1
1.5051627801819254,0.08241137491360147,0,1
1.5046993636080663,0.08205834070254334,0,1
1.5042502073680106,0.08168733295717479,0,1
1.5038160081218144,0.08129892712597855,0,1
1.5033974393306133,0.08089372564259405,0,1
1.5029951502120553,0.08047235699141744,0,1
1.5026097647333372,0.08003547473279633,0,1
1.5022418806434061,0.07958375648933029,0,1
1.5018920685458246,0.07911790289485002,0,1
1.501560871013742,0.07863863650770501,0,1
1.5012488017483405,0.07814670069004548,0,1
1.500956344782063,0.0776428584548366,0,1
1.5006839537278585,0.07712789128239364,0,1
1.5004320510756097,0.0766025979082734,0,1
1.5002010275368338,0.07606779308440205,0,1
1.4999912414386727,0.07552430631536088,0,1
1.4998030181681112,0.07497298057179018,0,1
1.4996366496672908,0.0744146709829066,0,1
1.499492393980693,0.07385024351016203,0,1
1.499370474854903,0.0732805736041014,0,1
1.4992710813915682,0.0727065448465022,0,1
1.4991943677540946,0.07212904757990249,0,1
1.4991404529285328,0.07154897752664235,0,1
1.499109420539025,0.07096723439956133,0,1
1.4991013187181015,0.07038472050650615,0,1
1.4991161600320244,0.06980233935081374,0,1
1.4991539214612968,0.06922099422993985,0,1
1.4992145444363676,0.06864158683440702,0,1
1.4992979349284743,0.06806501584924497,0,1
1.499403963595487,0.06749217556009267,0,1
1.499532465982522,0.06692395446612405,0,1
1.4996832427770188,0.06636123390194869,0,1
1.4998560601178823,0.0658048866706251,0,1
1.5000506499582111,0.0652557756899068,0,1
1.500266710481049,0.0647147526538209,0,1
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

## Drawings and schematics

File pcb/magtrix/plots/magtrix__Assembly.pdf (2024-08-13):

# D96 Q26 Q28

D132 R54

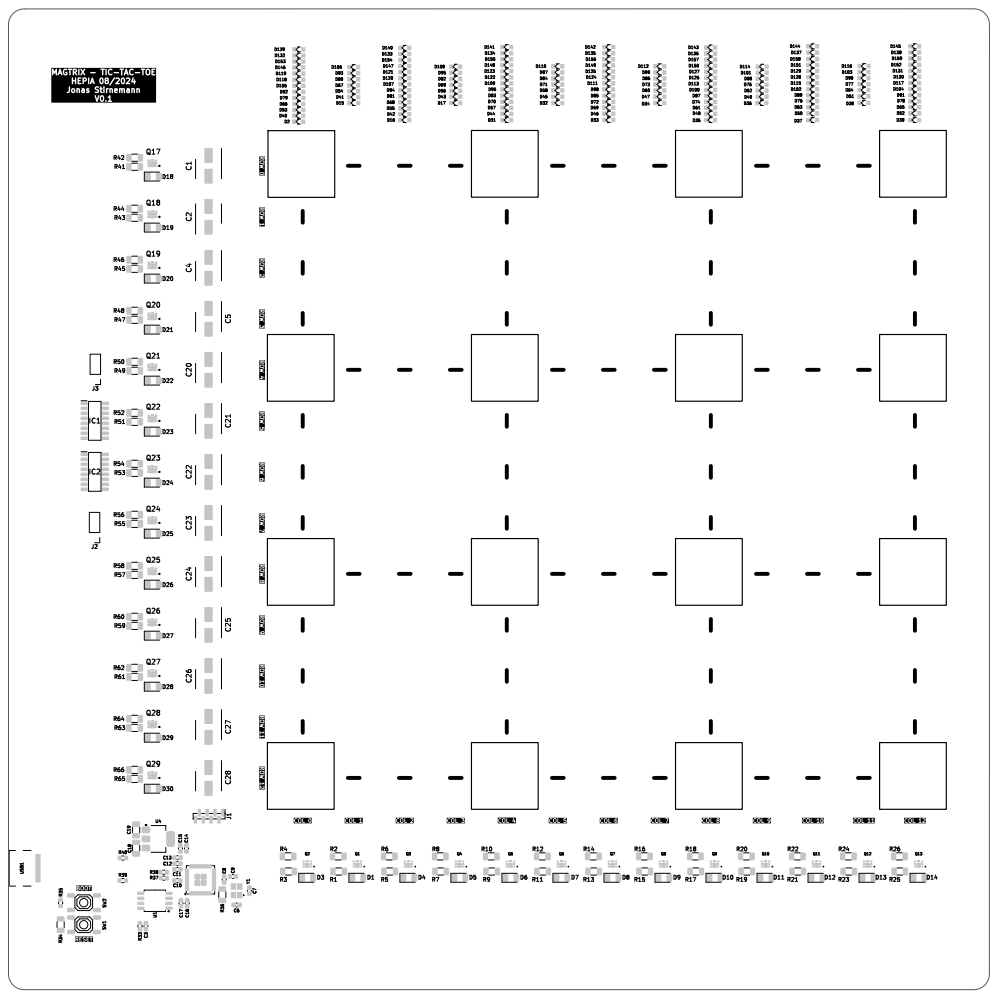
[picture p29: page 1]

Id: 1/1 Title: File: magtrix.kicad_pcb Sheet:

1 | 2 | 3 | 4 | 5 | 6 | 7 | 8 | 9 | 10 | 11 | 12 | 13 | 14 | 15 | 16 | 17 | 18 | 19 | 20 | 21 | 22 | 23

A

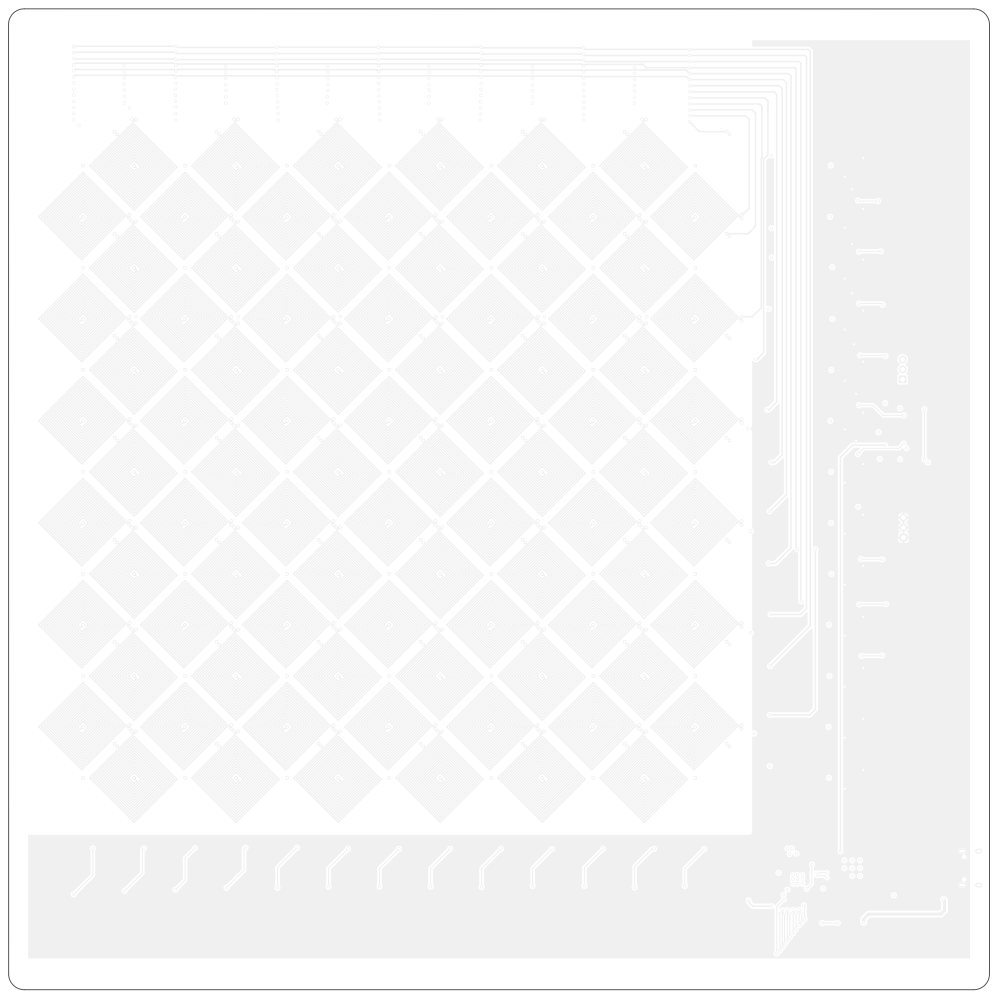
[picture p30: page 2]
IJK; P Date: KiCad E.D.A. 8.0.4 Size: A0; Rev:

Id: 1/1 Title: File: magtrix.kicad_pcb Sheet:

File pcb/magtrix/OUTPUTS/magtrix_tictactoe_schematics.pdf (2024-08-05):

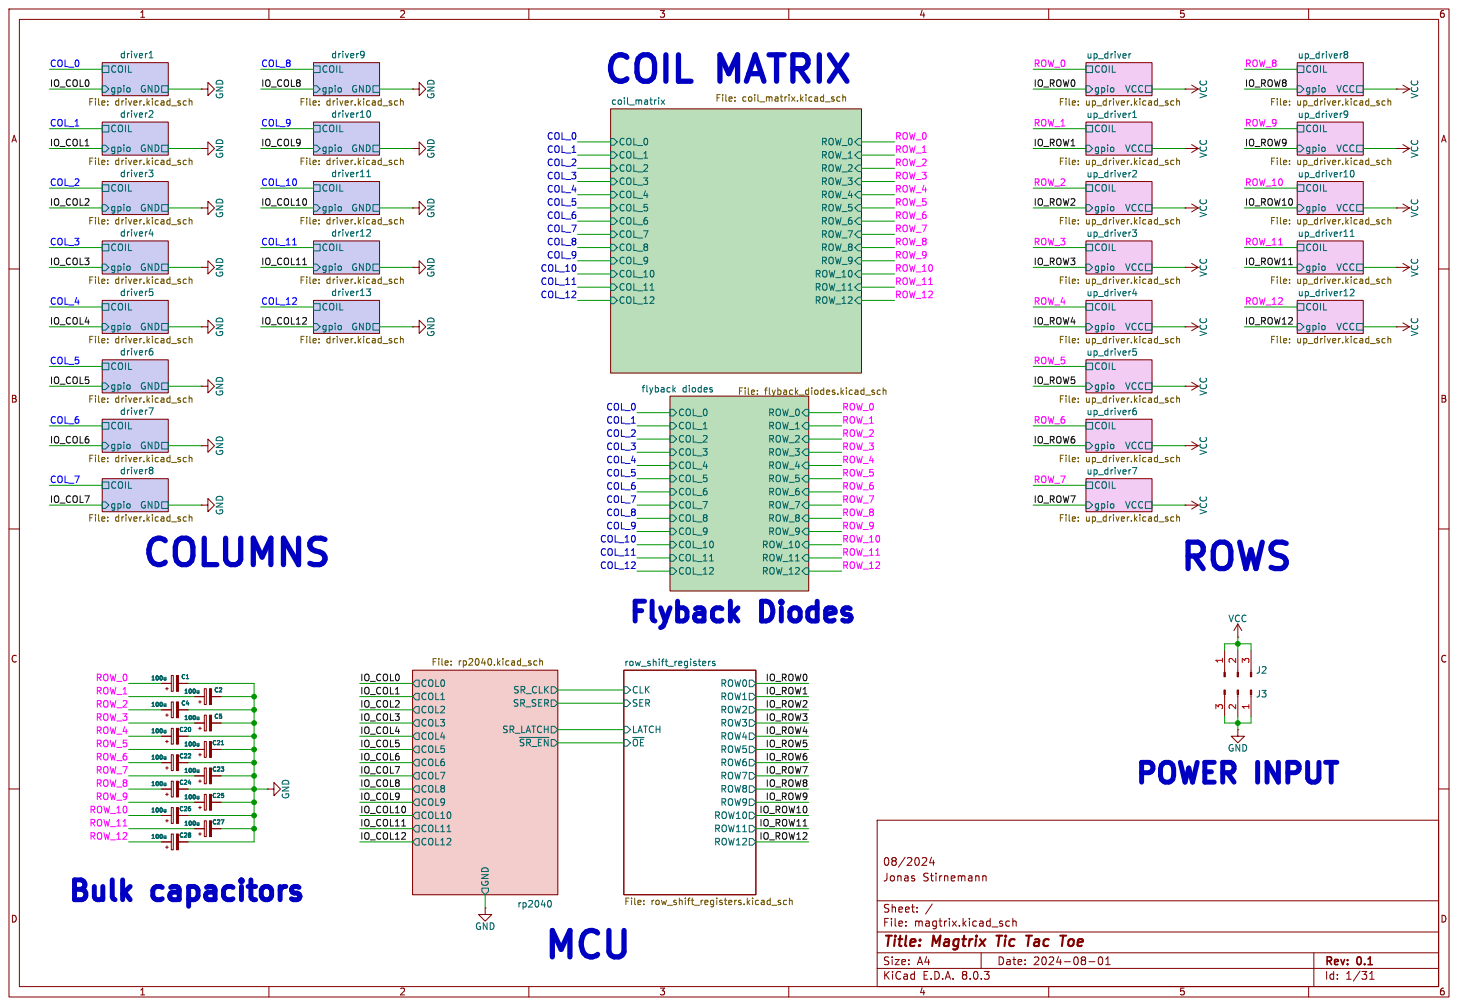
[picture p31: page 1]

File: magtrix.kicad_sch Sheet: / Jonas Stirnemann

Id: 1/31 Title: Magtrix Tic Tac Toe

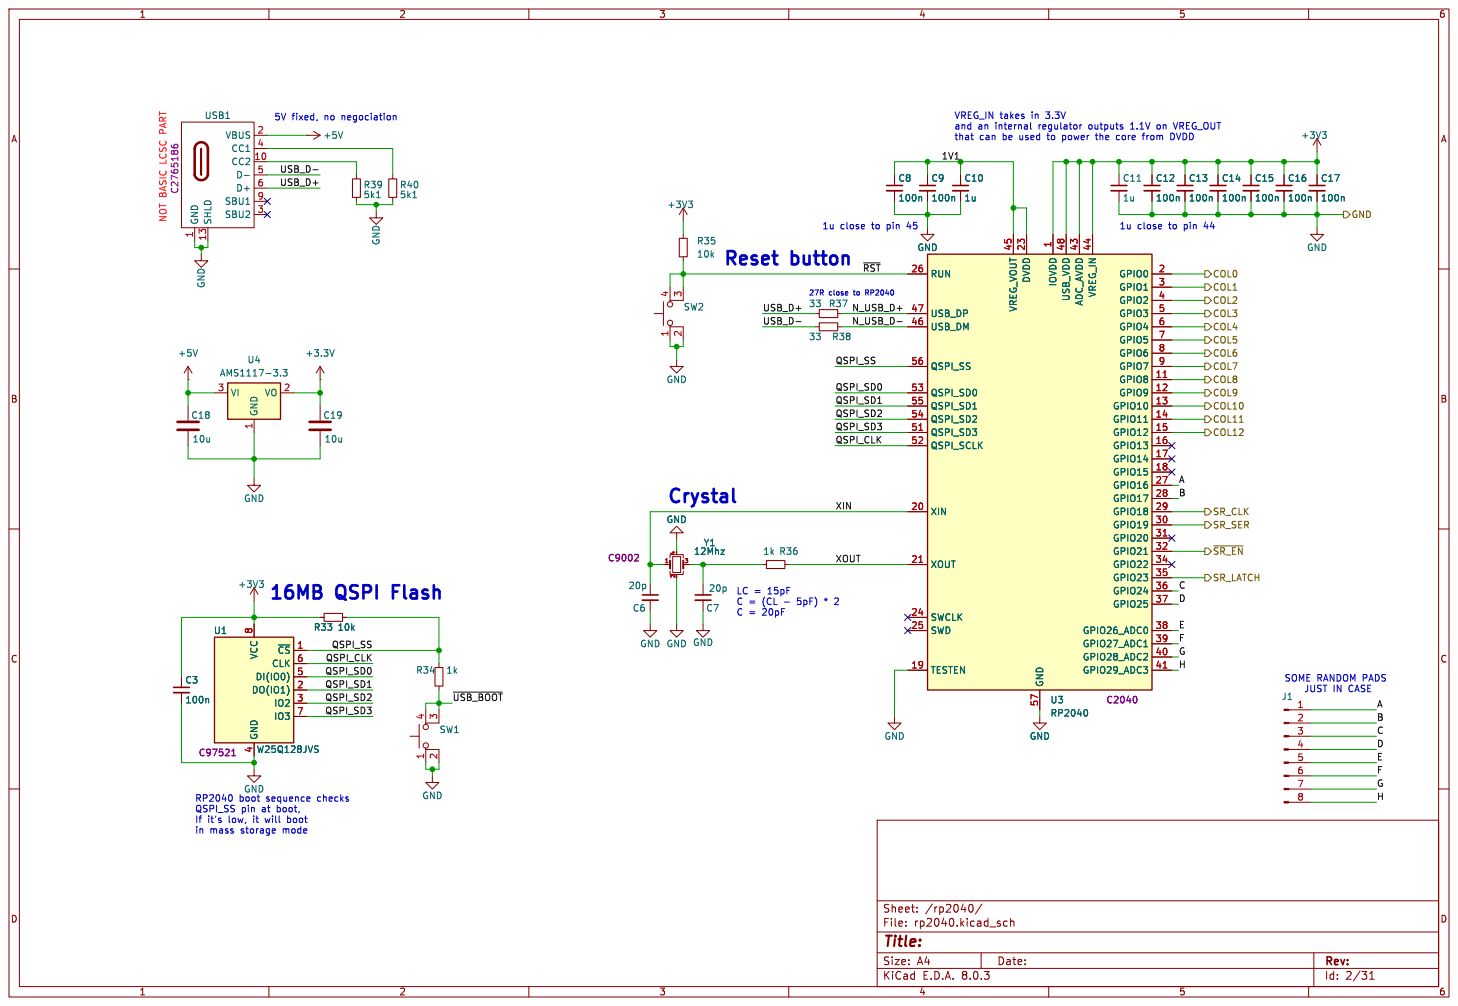
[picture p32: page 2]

VREG_IN takes in 3.3V
that can be used to power the core from DVDD

1u close to pin 45 Crystal GND
Reset button

If it's low, it will boot
in mass storage mode

File: coil_matrix.kicad_sch Sheet: /coil_matrix/ Jonas Stirnemann

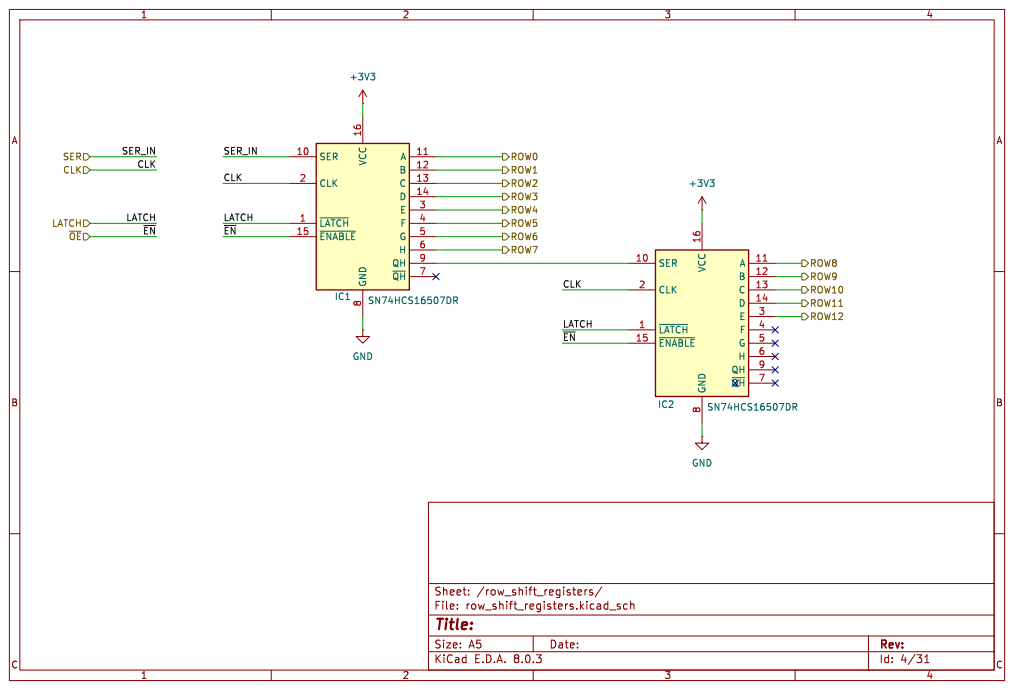
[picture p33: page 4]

Id: 4/31 Title: File: row_shift_registers.kicad_sch Sheet: /row_shift_registers/

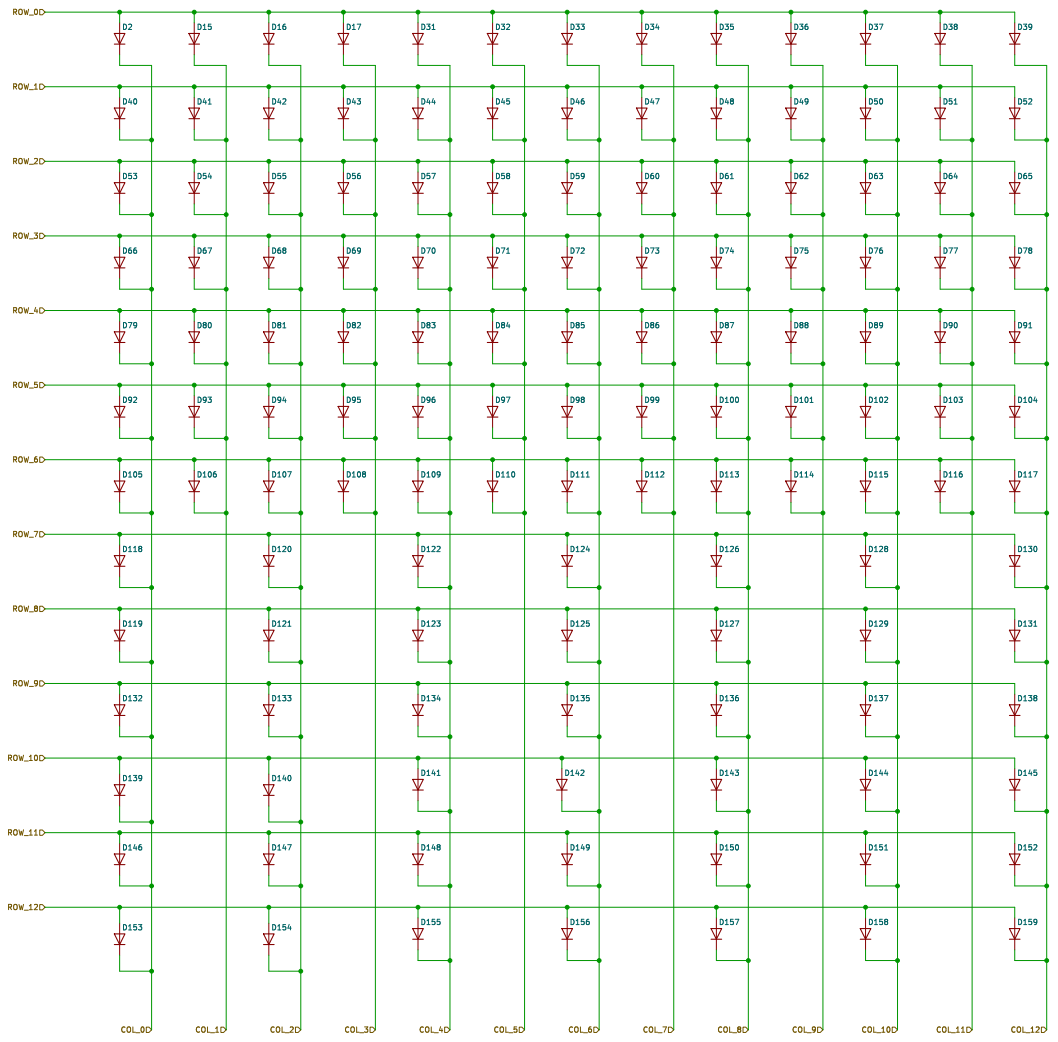
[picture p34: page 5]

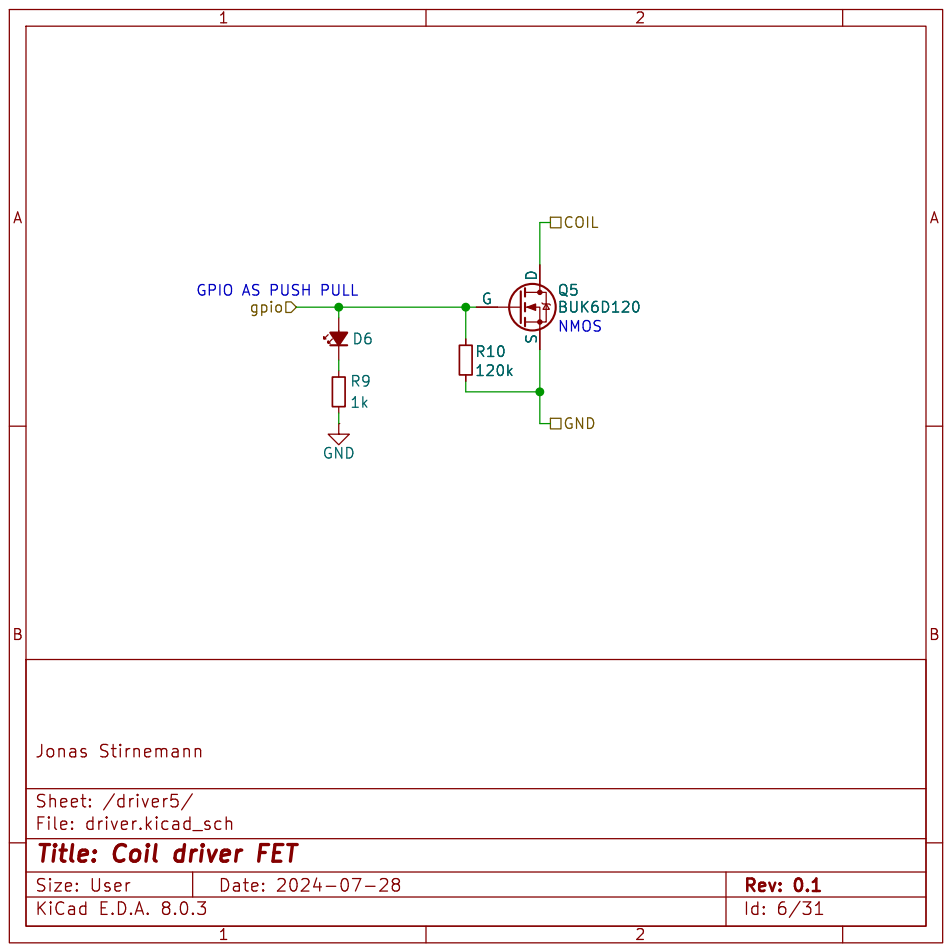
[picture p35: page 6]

Id: 6/31 Title: Coil driver FET

Id: 7/31 Title: Coil driver FET

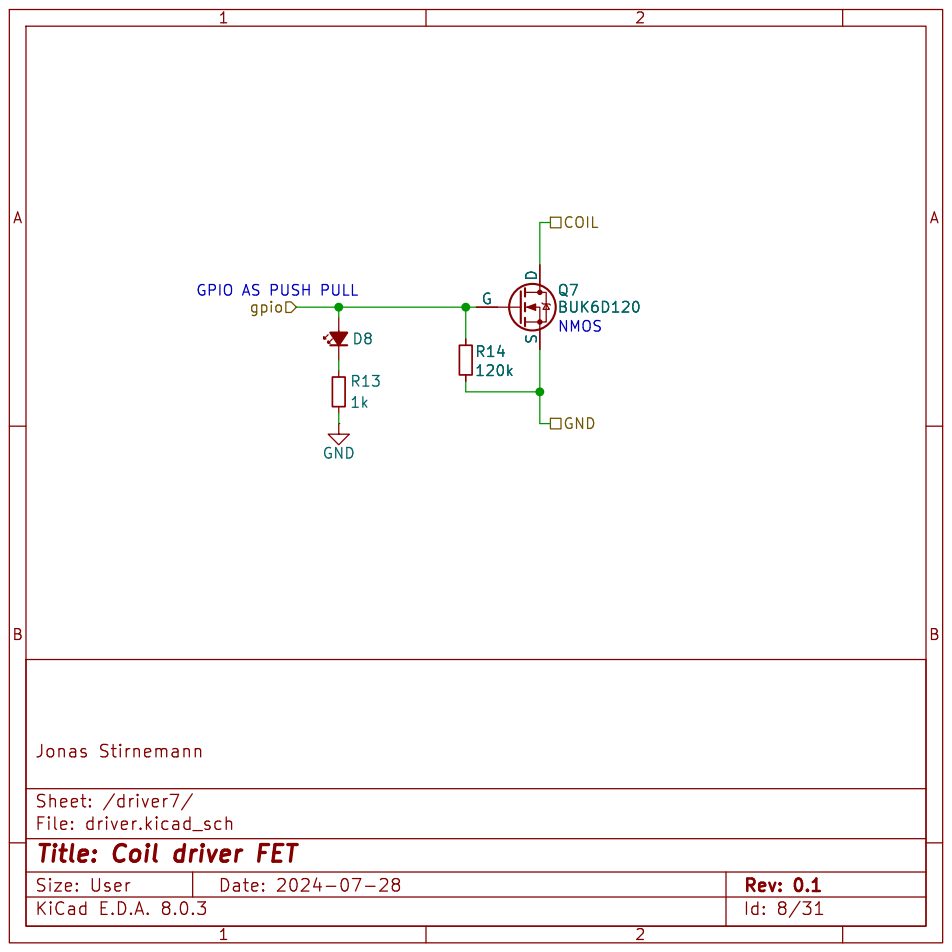
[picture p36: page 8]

Id: 8/31 Title: Coil driver FET

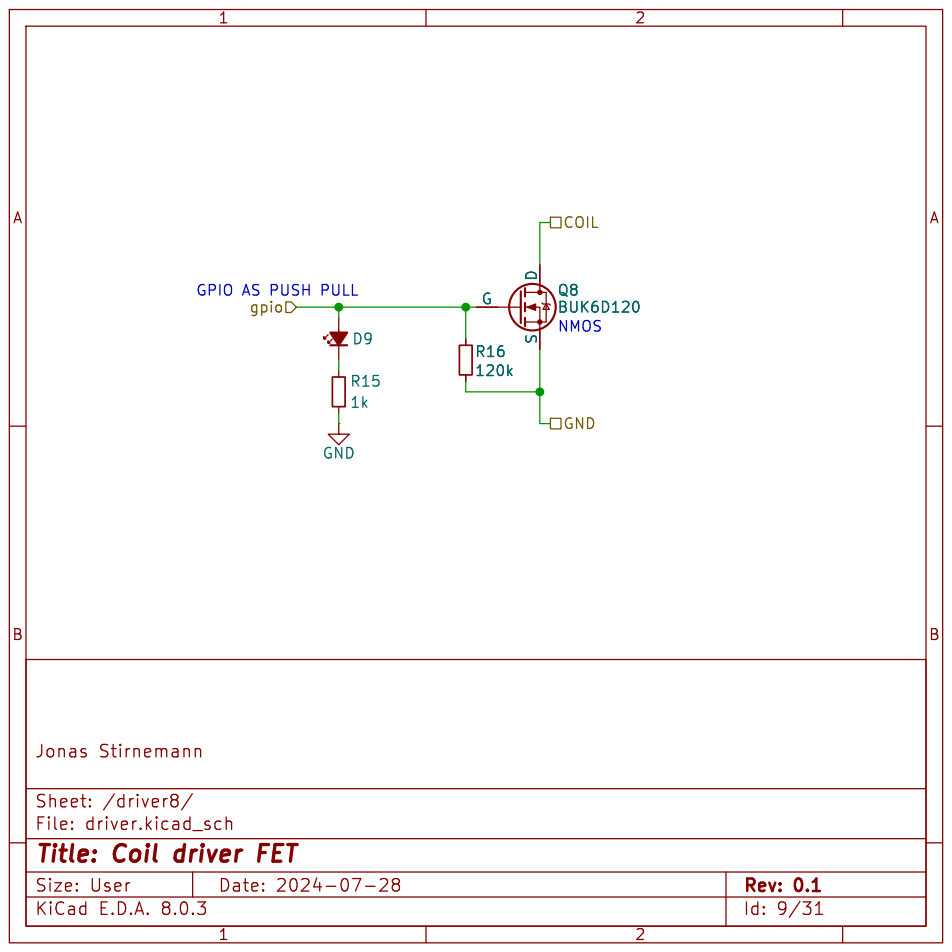
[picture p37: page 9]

Id: 9/31 Title: Coil driver FET

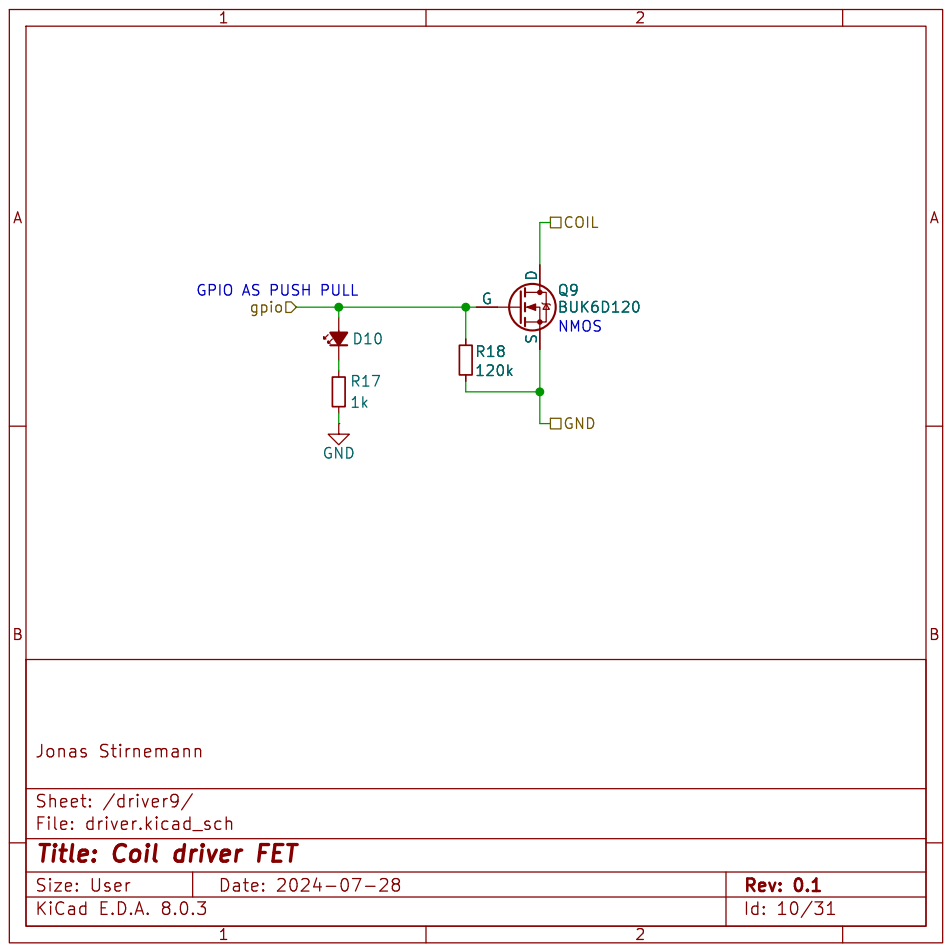
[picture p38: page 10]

Id: 10/31 Title: Coil driver FET

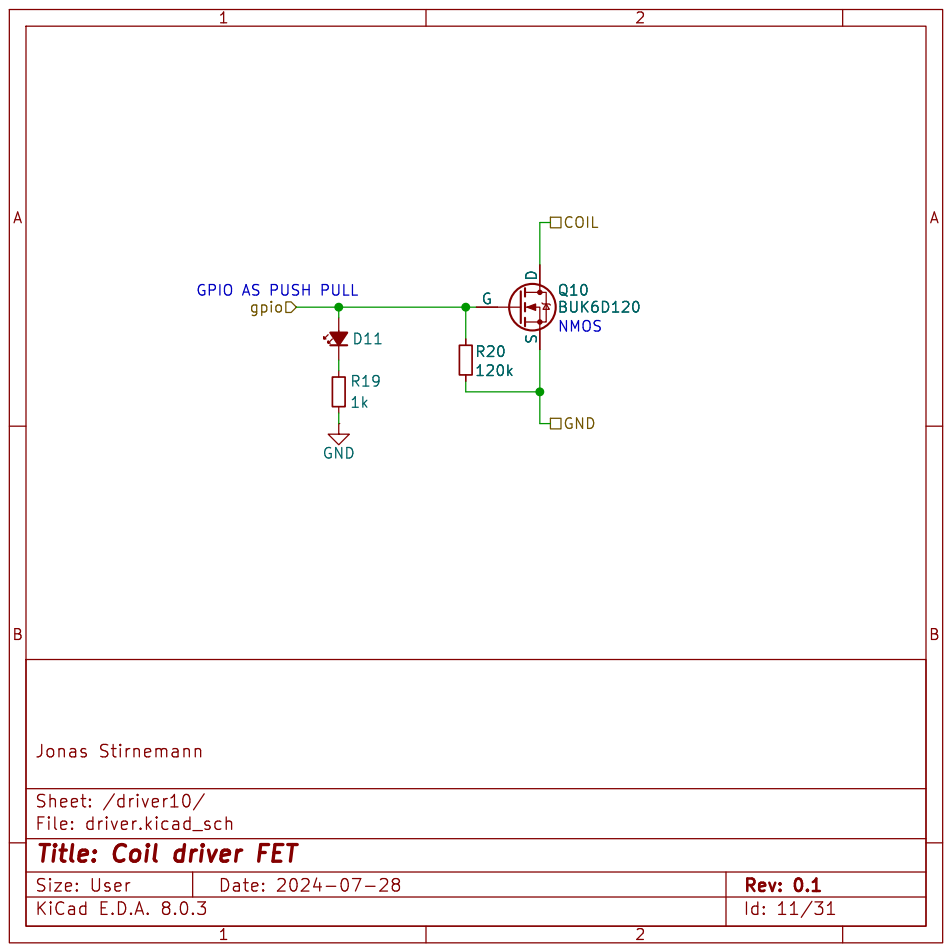
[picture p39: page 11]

Id: 11/31 Title: Coil driver FET

Id: 12/31 Title: Coil driver FET

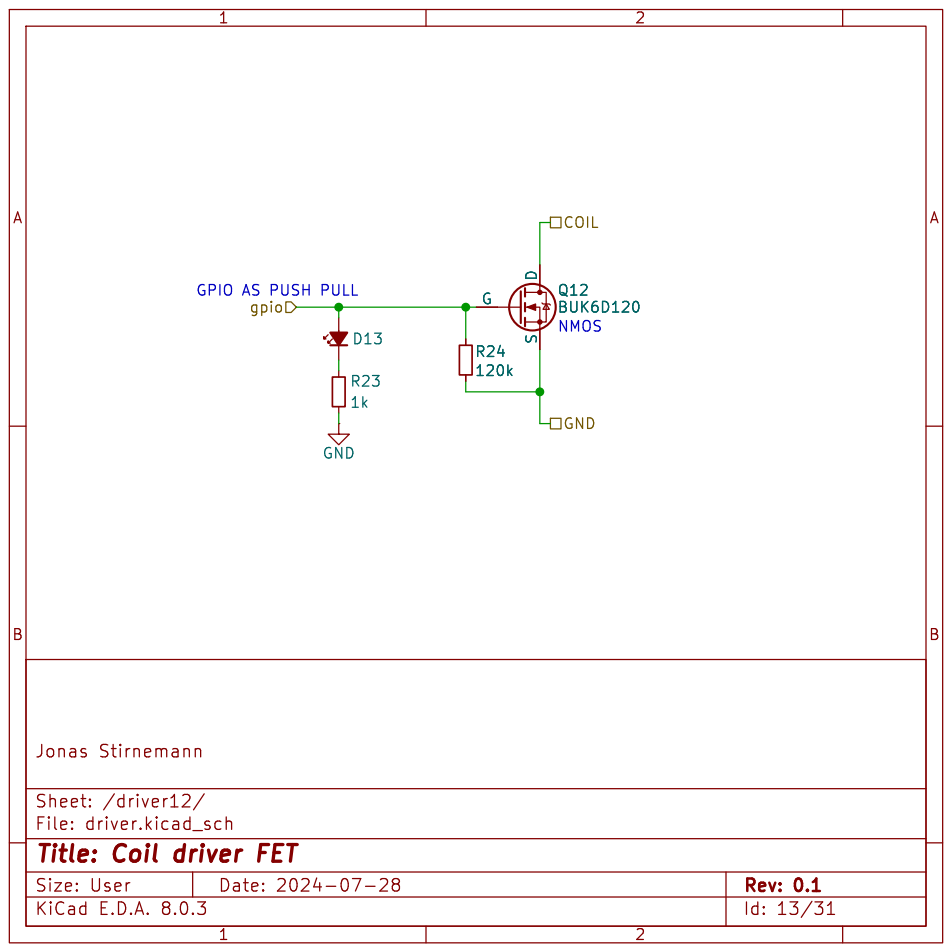
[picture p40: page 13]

Id: 13/31 Title: Coil driver FET


Id: 14/31 Title: Coil driver FET


Id: 18/31 Title: Coil driver FET

Id: 19/31 Title: Coil driver FET


gpio GPIO AS OPEN DRAIN


gpio GPIO AS OPEN DRAIN


gpio GPIO AS OPEN DRAIN

gpio GPIO AS OPEN DRAIN


gpio GPIO AS OPEN DRAIN


gpio GPIO AS OPEN DRAIN


gpio GPIO AS OPEN DRAIN


gpio GPIO AS OPEN DRAIN

gpio GPIO AS OPEN DRAIN


gpio GPIO AS OPEN DRAIN


gpio GPIO AS OPEN DRAIN


gpio GPIO AS OPEN DRAIN

gpio GPIO AS OPEN DRAIN


Id: 37/31 Title: Coil driver FET


Id: 38/31 Title: Coil driver FET

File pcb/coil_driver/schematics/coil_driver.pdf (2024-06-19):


File: coil_driver.kicad_sch Sheet: / Jonas Stirnemann

Id: 1/11 Title: Testing linear coils


Id: 2/11 Title: Coil driver File: single_coil.kicad_sch Sheet: /coil_driver/ Jonas Stirnemann D4 VCC


Id: 3/11 Title: Coil driver File: single_coil.kicad_sch Sheet: /coil_driver1/ Jonas Stirnemann D6 VCC


Id: 4/11 Title: Coil driver File: single_coil.kicad_sch Sheet: /coil_driver2/ Jonas Stirnemann D9 VCC


Id: 5/11 Title: Coil driver File: single_coil.kicad_sch Sheet: /coil_driver3/ Jonas Stirnemann D12 VCC


Id: 6/11 Title: Coil driver File: single_coil.kicad_sch Sheet: /coil_driver4/ Jonas Stirnemann D15 VCC


Id: 7/11 Title: Coil driver File: single_coil.kicad_sch Sheet: /coil_driver5/ Jonas Stirnemann D18 VCC


File: coil_module1.kicad_sch Sheet: /coil_module1/ Jonas Stirnemann

Id: 8/11 Title: Coil module 1


File: coil_module2.kicad_sch Sheet: /coil_module2/ Jonas Stirnemann

Id: 9/11 Title: Coil module 2


File: coil_module3.kicad_sch Sheet: /coil_module3/ Jonas Stirnemann

Id: 10/11 Title: Coil module 3


File: coil_module4.kicad_sch Sheet: /coil_module4/ Jonas Stirnemann

Id: 11/11 Title: Coil Module 4

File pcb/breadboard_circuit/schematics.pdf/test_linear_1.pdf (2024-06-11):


Id: 1/1 Title: File: test_linear_1.kicad_sch Sheet: /

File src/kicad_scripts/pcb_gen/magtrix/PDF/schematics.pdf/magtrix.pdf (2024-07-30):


Id: 1/37 Title: File: magtrix.kicad_sch Sheet: / CLR

27R close to RP2040 16MB QSPI Flash NOT BASIC LCSC PART

VREG_IN takes in 3.3V
that can be used to power the core from DVDD
COL8 COL3 COL0 COL1 ~{SR_EN}
COL2 SR_CLK

RP2040 boot sequence checks QSPI_SS pin at boot,

If it's low, it will boot
in mass storage mode

Id: 2/37 Title: File: rp2040.kicad_sch Sheet: /rp2040/


File: coil_matrix.kicad_sch Sheet: /coil_matrix/ Jonas Stirnemann


Id: 4/37 Title: File: row_shift_registers.kicad_sch Sheet: /row_shift_registers/ GND


Id: 6/37 Title: Coil driver FET


Id: 7/37 Title: Coil driver FET

Id: 8/37 Title: Coil driver FET


Id: 9/37 Title: Coil driver FET

Id: 10/37 Title: Coil driver FET


Id: 11/37 Title: Coil driver FET


Id: 12/37 Title: Coil driver FET

Id: 13/37 Title: Coil driver FET


Id: 14/37 Title: Coil driver FET


Id: 15/37 Title: Coil driver FET

Id: 16/37 Title: Coil driver FET


Id: 17/37 Title: Coil driver FET


Id: 18/37 Title: Coil driver FET

Id: 19/37 Title: Coil driver FET


gpio GPIO AS OPEN DRAIN


gpio GPIO AS OPEN DRAIN

gpio GPIO AS OPEN DRAIN


gpio GPIO AS OPEN DRAIN


gpio GPIO AS OPEN DRAIN

gpio GPIO AS OPEN DRAIN


gpio GPIO AS OPEN DRAIN


gpio GPIO AS OPEN DRAIN

gpio GPIO AS OPEN DRAIN


gpio GPIO AS OPEN DRAIN

gpio GPIO AS OPEN DRAIN


gpio GPIO AS OPEN DRAIN


gpio GPIO AS OPEN DRAIN

gpio GPIO AS OPEN DRAIN


gpio GPIO AS OPEN DRAIN


gpio GPIO AS OPEN DRAIN

Id: 37/37 Title: Coil driver FET


Id: 38/37 Title: Coil driver FET

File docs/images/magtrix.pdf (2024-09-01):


IO_COL0 ROW_1 ROW_0 ROW_6
gpio GND
IO_ROW9 POWER INPUT
VCC VCC

File: magtrix.kicad_sch Sheet: / Jonas Stirnemann

Id: 1/31 Title: Magtrix Tic Tac Toe


that can be used to power the core from DVDD NOT BASIC LCSC PART

27R close to RP2040 16MB QSPI Flash

JUST IN CASE RP2040 boot sequence checks QSPI_SS pin at boot,

If it's low, it will boot

Id: 2/31 Title: File: rp2040.kicad_sch Sheet: /rp2040/

File: coil_matrix.kicad_sch Sheet: /coil_matrix/ Jonas Stirnemann


Id: 4/31 Title: File: row_shift_registers.kicad_sch Sheet: /row_shift_registers/



Id: 6/31 Title: Coil driver FET

Id: 7/31 Title: Coil driver FET


Id: 8/31 Title: Coil driver FET


Id: 9/31 Title: Coil driver FET


Id: 10/31 Title: Coil driver FET


Id: 11/31 Title: Coil driver FET

Id: 12/31 Title: Coil driver FET


Id: 13/31 Title: Coil driver FET


Id: 14/31 Title: Coil driver FET


Id: 18/31 Title: Coil driver FET

Id: 19/31 Title: Coil driver FET


gpio GPIO AS OPEN DRAIN


gpio GPIO AS OPEN DRAIN


gpio GPIO AS OPEN DRAIN

gpio GPIO AS OPEN DRAIN


gpio GPIO AS OPEN DRAIN


gpio GPIO AS OPEN DRAIN


gpio GPIO AS OPEN DRAIN


gpio GPIO AS OPEN DRAIN

gpio GPIO AS OPEN DRAIN


gpio GPIO AS OPEN DRAIN


gpio GPIO AS OPEN DRAIN


gpio GPIO AS OPEN DRAIN

gpio GPIO AS OPEN DRAIN


Id: 37/31 Title: Coil driver FET


Id: 38/31 Title: Coil driver FET

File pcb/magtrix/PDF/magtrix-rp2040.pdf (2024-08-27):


that can be used to power the core from DVDD NOT BASIC LCSC PART

1u close to pin 44 Reset button

27R close to RP2040 16MB QSPI Flash

JUST IN CASE RP2040 boot sequence checks QSPI_SS pin at boot,

If it's low, it will boot
in mass storage mode

Id: 2/31 Title: File: rp2040.kicad_sch Sheet: /rp2040/

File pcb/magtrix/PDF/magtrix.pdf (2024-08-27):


File: magtrix.kicad_sch Sheet: / Jonas Stirnemann

Id: 1/31 Title: Magtrix Tic Tac Toe


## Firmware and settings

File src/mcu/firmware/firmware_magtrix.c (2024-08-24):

/**
 * Magtrix firmware
 * Author: Jonas Stirnemann

 * Date: 26/07/2024
 *
 *
 * These is the full firmware to put on the RP2040 Edge A and B
 * The firmware of the RP edge C is different and is in another file
 *
 *
 * Source for SMP support (Important docs too)
 * https://github.com/Evlers/pico-freertos/tree/master

 */


#include <stdio.h>
#include <stdlib.h>
#include <string.h>
#include <tusb.h>

// ---
#include "FreeRTOSConfig.h"
// ---
#include "hardware/clocks.h"
#include "hardware/dma.h"
#include "hardware/irq.h"
#include "hardware/pio.h"
#include "hardware/spi.h"
#include "hardware/structs/clocks.h"
#include "hardware/structs/pll.h"
#include "pico/binary_info.h"
#include "pico/stdlib.h"
// ---
#include "FreeRTOS.h"
#include "mag_pwm.h"
#include "queue.h"
#include "task.h"
// ---


#define LED_STATUS_PIN 25

// ! PWM GENERATORS
#define PWM_FREQ  25000 // 25 Khz prefered in datasheet
#define NB_PWMS	  13
#define BASE_DUTY 0.0
typedef enum
{
	PWM_0  = 0,
	PWM_1  = 1,
	PWM_2  = 2,
	PWM_3  = 3,
	PWM_4  = 4,
	PWM_5  = 5,
	PWM_6  = 6,
	PWM_7  = 7,
	PWM_8  = 8,
	PWM_9  = 9,
	PWM_10 = 10,
	PWM_11 = 11,
	PWM_12 = 12,
} PWM_PINS;
const PWM_PINS pwms_gpios[NB_PWMS] = { PWM_0, PWM_1, PWM_2, PWM_3,	PWM_4,	PWM_5, PWM_6,
									   PWM_7, PWM_8, PWM_9, PWM_10, PWM_11, PWM_12 };


#define NB_ROWS 12
typedef enum
{
	ROW_0  = 16,
	ROW_1  = 17,
	ROW_2  = 24,
	ROW_3  = 25,
	ROW_4  = 26,
	ROW_5  = 27,
	ROW_6  = 28,
	ROW_7  = 29,
	ROW_8  = 18,
	ROW_9  = 19,
	ROW_10 = 21,
	ROW_11 = 23
} col_pins_t;
col_pins_t rows_gpios[NB_ROWS]
  = { ROW_0, ROW_1, ROW_2, ROW_3, ROW_4, ROW_5, ROW_6, ROW_7, ROW_8, ROW_9, ROW_10, ROW_11 };


// ! TASKS
typedef struct
{
	int frequency; // Hz
} task_arg;


typedef struct
{
	int			frequency; // Hz
	mag_pwm_t*	pwms;
	col_pins_t* rows_gpios;
} coils_args_t;


void t_debug(void* p);
void t_coils(void* p);

static void od_gpio_down(uint gpio);
static void od_gpio_up(uint gpio);

// ! FUNCTIONS
// ! PWM
int main()
{
	stdio_init_all();
	sleep_ms(2000);

	// ! PWM (COLS)
	mag_pwm_t pwms[NB_PWMS];
	for (uint8_t i = 0; i < NB_PWMS; i++)
	{
		mag_pwm_init_from_gpio(&pwms[i], pwms_gpios[i], PWM_FREQ, 0.0);
		mag_pwm_enable(&pwms[i]);
	}

	// ! SET GPIOS HIGH (transistors disabled)
	for (uint8_t i = 0; i < NB_ROWS; i++)
		od_gpio_up(rows_gpios[i]);


	TaskHandle_t coils_handle;
	UBaseType_t	 coils_affinity_mask;
	coils_args_t arg_coils = { .frequency = 1, .pwms = pwms, .rows_gpios = rows_gpios };
	xTaskCreate(t_coils, "COILS", 1024, &arg_coils, 10, &coils_handle);
	coils_affinity_mask = 0x02;
	vTaskCoreAffinitySet(coils_handle, coils_affinity_mask);


	TaskHandle_t debug_handle;
	UBaseType_t	 spi_write_affinity_mask;
	task_arg	 arg_debug = { .frequency = 50 };
	xTaskCreate(t_debug, "DEBUG", 512, &arg_debug, 1, &debug_handle);
	spi_write_affinity_mask = 0x01;
	vTaskCoreAffinitySet(debug_handle, spi_write_affinity_mask);


	vTaskStartScheduler();

	while (true)
		;
}

// Stack overflow hook
void vApplicationStackOverflowHook(TaskHandle_t xTask, char* pcTaskName)
{
	(void)xTask;
	(void)pcTaskName;

	gpio_put(LED_STATUS_PIN, 1);
	configASSERT(0);
}

// Malloc failed hook
void vApplicationMallocFailedHook(void)
{
	gpio_put(LED_STATUS_PIN, 1);
	configASSERT(0);
}

/**
 * @brief Just printing some debugging informations
 */
void t_debug(void* p)
{
	task_arg* a		 = (task_arg*)p;
	uint64_t  period = 1000 / a->frequency;

	while (true)
	{
		printf("t_debug : core %d\n", get_core_num());
		vTaskDelay(period * portTICK_PERIOD_MS);
	}
}

void t_coils(void* p)
{
	coils_args_t* a			 = (coils_args_t*)p;
	uint64_t	  period	 = 1000 / a->frequency;
	mag_pwm_t*	  pwms		 = a->pwms;
	col_pins_t*	  rows_gpios = a->rows_gpios;
	uint8_t		  index_col	 = 0;
	uint8_t		  index_row	 = 0;


	while (true)
	{
		// ! Power the row
		// for (uint8_t i = 0; i < NB_ROWS; i++)
		//	od_gpio_up(rows_gpios[i]);

		od_gpio_down(rows_gpios[0]);

		// Turn off every coils
		for (uint8_t i = 0; i < NB_PWMS; i++)
			mag_pwm_set_duty(&pwms[i], 0.0);

		// ! Power the coil
		mag_pwm_set_duty(&pwms[1], 0.1);


		if (index_col >= NB_PWMS - 1)
			index_col = 0;
		else
			index_col++;

		if (index_row >= NB_ROWS - 1)
			index_row = 0;
		else
			index_row++;

		vTaskDelay(period * portTICK_PERIOD_MS);

		printf("t_coils : core %d\n", get_core_num());
	}
}


static void od_gpio_down(uint gpio)
{
	// Set the GPIO as output
	gpio_init(gpio);
	gpio_set_dir(gpio, GPIO_OUT);
	gpio_put(gpio, 0);
}

/**
 * There is no open drain mode
 * on the RP2040 so we just set the GPIO as input
 * to simulate the open drain mode
 */
static void od_gpio_up(uint gpio)
{
	// ? Set the GPIO as input
	gpio_init(gpio);
	gpio_set_dir(gpio, GPIO_IN);

	// ? disable the pulls
	gpio_set_pulls(gpio, false, false);
}

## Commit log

2024-05-23 Test SVG and simu, nope
    [driving.kicad_pcb, driving.kicad_sch, planning.csv]
2024-05-28 Added week_3
    [driving.kicad_pcb]
2024-06-11 Week 4
    [coil_driver.kicad_pcb, coil_driver.kicad_sch, linear_pmos.kicad_pcb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]
2024-06-13 Before destroying
    [coil_driver.kicad_sch, linears.kicad_pcb, linears.kicad_sch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]
2024-06-13 Finished schematics and began PCB, only rules for now
    [coil_driver.kicad_pcb, coil_driver.kicad_sch, coil_module1.kicad_sch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]
2024-06-13 Began PCB
    [coil_driver.kicad_pcb, coil_driver.kicad_sch, single_coil.kicad_sch]
2024-06-15 Before changing coils to footprints
    [coil_driver.kicad_pcb, coil_driver.kicad_sch, coil_module1.kicad_sch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]
2024-06-18 Almost finished PCB
    [coil_driver.kicad_pcb, coil_module1.kicad_sch, coil_module2.kicad_sch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]
2024-06-19 PCB Should be finished
    [coil_driver.kicad_pcb, coil_driver.kicad_sch]
2024-06-19 Finished PCB
    [bom.csv, coil_driver.kicad_pcb, designators.csv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]
2024-06-20 Added basic chess board with chessground
2024-06-25 Fixed tictactoe
    [bomlist_coil_tester_stirnemann.csv, bomlist_coil_tester_stirnemann_mouser.csv, coil_driver.kicad_sch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]
2024-07-03 Added empty coils
    [only_coils.kicad_pcb, only_coils.kicad_sch]
2024-07-03 PCB barely started
    [only_coils.kicad_pcb, only_coils.kicad_sch]
2024-07-04 Added layered PCB
    [layered.kicad_pcb, layered.kicad_sch, linear.kicad_pcb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]
2024-07-09 Added leyered project
    [layered.kicad_pcb]
2024-07-09 Added finished layered PCB
    [bom.csv, designators.csv, layered.kicad_pcb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]
2024-07-09 Added second pcb
    [sub_coils.kicad_pcb, sub_coils.kicad_sch]
2024-07-10 Added small script for square coils
    [bom.csv, designators.csv, layered.kicad_pcb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]
2024-07-11 Added finished linear coils PCB
    [bom.csv, designators.csv, layered.kicad_pcb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]
2024-07-19 Added sub square PCB
    [bom.csv, designators.csv, layered.kicad_pcb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]
2024-07-19 Added corrected script for footprint squares
2024-07-23 Added schematics script before becomming class
    [driving.kicad_pcb, driving.kicad_sch, test_project.kicad_pcb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]
2024-07-23 Added basic classed compenent Matrix Maker
    [test_project.kicad_sch]
2024-07-23 Before turning components in schematics maker
    [test_project.kicad_sch]
2024-07-23 Working component matrix schematics drawer
    [test_project.kicad_sch]
2024-07-23 Fixed scalability issue
    [test_project.kicad_sch]
2024-07-24 Moved PCB test, added basic pcbnew script, footprint script is not last one
    [test_project.kicad_pcb, test_project.kicad_sch]
2024-07-28 Footprint placement seems ok, but too much top coils + orientations broken
2024-07-28 Added test project, lets go by hand for now
    [coils_layout.csv, test_project.kicad_sch]
2024-07-28 Closer coils like in test PCB
2024-07-28 Added almost finished schematics magtrix
    [bemf.kicad_sch, coil_matrix.kicad_sch, coils_layout.csv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]
2024-07-30 Finished schematics and footprints, need to redo the placement
    [coil_matrix.kicad_sch, driver.kicad_sch, magtrix.kicad_sch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]
2024-07-30 Changed shift registers to open drain ones
    [magtrix.kicad_sch, row_shift_registers.kicad_sch, rp2040.kicad_sch]
2024-07-30 Auto pcb coils layout done
2024-07-30 Added auto layout scripts
    [bemf.kicad_sch, coil_matrix.kicad_sch, coils_layout.csv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]
2024-07-30 Fixed layout pcb coils
2024-08-05 Added finished PCB
    [basket_magtrix_mouser.xls, bemf.kicad_sch, bom.csv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]
2024-08-13 Added pwm code
    [magtrix-all-pos.csv]
2024-08-15 Added pwm and shift register
2024-08-20 Added almost finished memoire, need cover photo
    [planning.csv]
2024-08-27 Added poster pptx and pdf
    [coils_layout.csv, magtrix.kicad_sch, sub_squares.kicad_pcb]
